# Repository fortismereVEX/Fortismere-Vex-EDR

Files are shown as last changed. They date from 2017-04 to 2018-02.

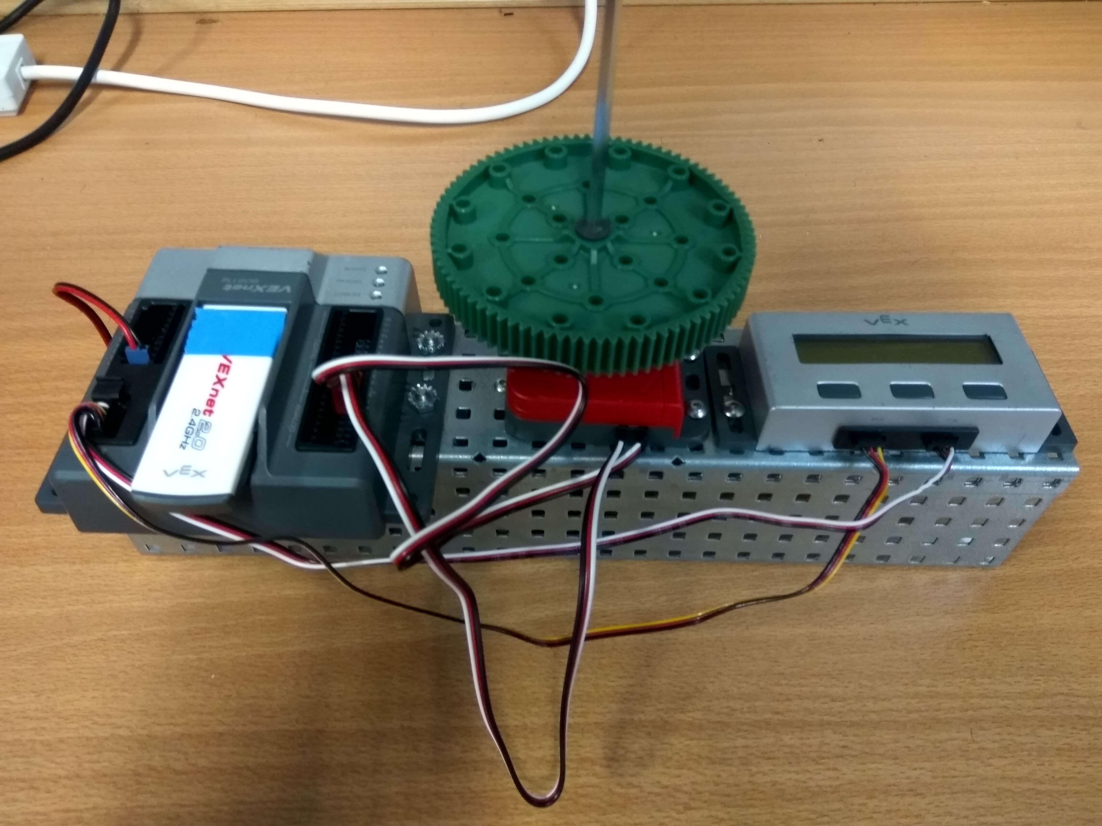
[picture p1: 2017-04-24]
zone/notebook/Resources/photos/PID Control.jpg

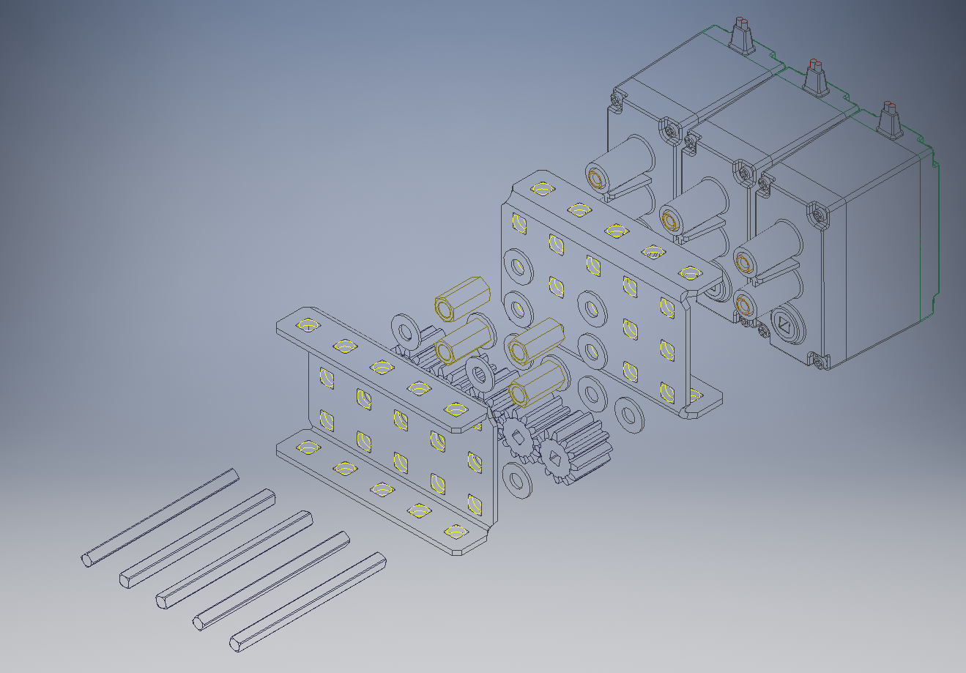
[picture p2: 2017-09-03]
zone/notebook/Renders and other cad stuff/Motor Block/Pictures and renders/Motor Block exploded view.PNG

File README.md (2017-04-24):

# Fortismere-Vex-EDR

Repo containing the various programs and tests for our Vex Robotics team, in addition to assorted files related to our engineering notebook.

##### /starstruck is for the 2016/2017 competition - Starstruck https://www.youtube.com/watch?v=0t2zstQ84Tw&t=1s
##### /zone is for the 2017/2018 competition  - In the Zone https://www.youtube.com/watch?v=1Yo_mlR1VJU

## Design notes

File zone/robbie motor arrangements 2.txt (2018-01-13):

1: mogo lift
2: claw left
3: left lift 1
4: exp 1 
5: exp 2
6: exp 3
7: exp 4
8: right lift 1
9: claw right
10: cone intake

expander:
1: drive right middle + drive right back
2: drive left middle + drive left back
3: left lift 2
4: right lift 2

sensors:
analogue:
2: left lift
3: right lift

digital:
2: + 3: left
4 + 5: right

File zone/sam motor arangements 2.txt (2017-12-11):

1 : arm left
2 : drive front left
3 : mogo right
4 : exp 1 
5 : exp 2
6 : exp 3
7 : exp 4
8 : lift 1
9 : drive front right
10: arm right

expander:
4 1: drive right middle + drive right back
5 2: drive left middle + drive left back
6 3: claw
7 4: mogo left

front left
middle left
back left
front right
middle right
back right
arm 1
arm 2
lift 1
claw
mogo 1
mogo 2

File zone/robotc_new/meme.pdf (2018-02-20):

File: C:\Users\admin\Documents\GitHub\Fortismere-Vex-EDR\zone\robotc_new\__basic.c

Page 1 of 11

#pragma config(Sensor, in1, left_line_sensor, | sensorLin

#pragma config(Sensor, in2, right_line_sensor, | sensorLi

#pragma config(Sensor, in3, claw_potent, | sensorPoten

#pragma config(Sensor, dgtl1, right_encoder, | sensorQuadE

#pragma config(Sensor, dgtl3, left_encoder, | sensorQuadE

#pragma config(Motor, port1, claw_1, | tmo

#pragma config(Motor, port2, right_front, | tmo

#pragma config(Motor, port3, left_front, | tmo

#pragma config(Motor, port4, arm_left_1, | tmo

#pragma config(Motor, port5, arm_left_2, | tmo

#pragma config(Motor, port6, arm_right_1, | tmo

#pragma config(Motor, port7, arm_right_2, | tmo

#pragma config(Motor, port8, right_back_middle,

#pragma config(Motor, port9, | left_back_middle,

#pragma config(Motor, port10, | claw_2, | tmo

//*!!Code automatically generated by 'ROBOTC' configuratio

#include "robotc_base_include.c"

#define max(x, a) (x > a ? x : a)

#define min(x, a) (x < a ? x : a) #define clamp(x, a, b) (min(b, max(a, x)))

float requested_left = 0.0;
float requested_right = 0.0;

float current_left = 0.0;
float current_right = 0.0;

float integral_left;
float integral_right;

float last_error_left;
float last_error_right;

float max_speed = 60.0;

void get_requested_delta(float *left, float *right) {

File: C:\Users\admin\Documents\GitHub\Fortismere-Vex-EDR\zone\robotc_new\__basic.c

Page 2 of 11

int r = (vexRT[Ch1] - vexRT[Ch3]);
int l = (vexRT[Ch1] + vexRT[Ch3]);

*left = abs(l) > 20 ? l : 0; *right = abs(r) > 20 ? r : 0;
}

float step_pid(float constant_p, float constant_i,
float constant_d,
float requested,
float current_value,
float *last_error,
float *integral) {
float error = current_value - requested;

float derivitive = error - *last_error; *last_error = error;

if (constant_i != 0 && abs(error) < 50) { *integral = *integral + error;
} else {
*integral = 0;
}

return constant_p * error + constant_i * *integral +
constant_d * derivitive;
}
task pid_loop() | {
// clear out the encoder
SensorValue[left_encoder] = 0; SensorValue[right_encoder] = 0;

current_left = 0;
current_right = 0;

File: C:\Users\admin\Documents\GitHub\Fortismere-Vex-EDR\zone\robotc_new\__basic.c

Page 3 of 11

requested_left = 0;
requested_right = 0;

last_error_left = 0;
last_error_right = 0;

integral_left = 0;
integral_right = 0;

bool reset = true;

while (true) {
current_left = SensorValue[left_encoder]; current_right = SensorValue[right_encoder];

/*
// user control stuff
float delta_requested_left = 0;
float delta_requested_right = 0;

get_requested_delta(&delta_requested_left, &delta_

if (delta_requested_left == 0 && delta_requested_r if (reset) {
requested_left = 0;
requested_right = 0;
SensorValue[left_encoder] = 0; SensorValue[right_encoder] = 0;

last_error_left = 0;
last_error_right = 0;

reset = false;
}
} else {
requested_left += delta_requested_left / 20; requested_right += delta_requested_right / 20;

File: C:\Users\admin\Documents\GitHub\Fortismere-Vex-EDR\zone\robotc_new\__basic.c

Page 4 of 11

reset = true;
}
*/

float new_left = step_pid(1, 0.0, 1, requested_left,
current_left,
&last_error_left,
&integral_left);
float new_right = step_pid(1, 0.0, 1, requested_right,
current_right,
&last_error_right,
&integral_right);

if (abs(new_left) < 20) new_left = 0;
if (abs(new_right) < 20) new_right = 0;

writeDebugStreamLine("r: %.2f %.2f c: %.2f %.2f e:

new_left = clamp(new_left, -max_speed, max_speed) new_right = clamp(new_right, -max_speed, max_speed

motor[right_front] = -new_right; motor[right_back_middle] = -new_right;

motor[left_front] = -new_left; motor[left_back_middle] = -new_left; }
}
void init() | {
stop_tasks_between_mode = true; }

void forward(float amount) {

File: C:\Users\admin\Documents\GitHub\Fortismere-Vex-EDR\zone\robotc_new\__basic.c

Page 5 of 11

requested_right -= amount;
requested_left += amount;
}
void turn(float amount) {
requested_right += amount; requested_left += amount;
}

bool at_dest(float threshold) {
if(abs(requested_left - current_left) < threshold | &&
abs(requested_right - current_right) < threshol integral_left = 0;
integral_right = 0;
return true;
}

return false;
}

void wait_for_dest(int timeout_ticks) { int curr = timeout_ticks;
while(!at_dest(20) && curr >= 0) { sleep(25);
--curr;
//clearLCDLine(0);
//displayLCDNumber(0, 0, curr, 2); }

if(curr == 0) {
displayLCDString(0, 0, "MISSED!!"); requested_left = current_left; requested_right = current_right; last_error_left = 0;
last_error_right = 0;
}
}

// positive for up, negative for down

File: C:\Users\admin\Documents\GitHub\Fortismere-Vex-EDR\zone\robotc_new\__basic.c

Page 6 of 11

void arm(int power) {
motor[arm_left_1] = -power;
motor[arm_left_2] = power;

motor[arm_right_1] = -power; motor[arm_right_2] = power; }

void claw(int power) {
motor[claw_1] = power;
motor[claw_2] = -power;
}

// TODO: all these timeouts are huge!!!
// The last one does at most 50 ticks before it gets to wh
task auton() | {
stopTask(pid_loop);
startTask(pid_loop);

SensorValue[claw_potent] = 0;

SensorValue[left_line_sensor] = 0; SensorValue[right_line_sensor] = 0;

int auton_option = 0;

bLCDBacklight = true;
clearLCDLine(0);
switch(auton_option) | {
case 0:
// Stack a cone onto the static goal

// move cone forward and then drive backwards

forward(100);
wait_for_dest(200);

File: C:\Users\admin\Documents\GitHub\Fortismere-Vex-EDR\zone\robotc_new\__basic.c

Page 7 of 11

forward(-100);
wait_for_dest(200);

arm(127);
sleep(300);
arm(0);
// claw close
claw(127);
sleep(500);
// arm down
claw(0);
arm(-127);
sleep(700)
arm(0);

// forwards
forward(100);
wait_for_dest(1000);

// claw close
claw(127);
sleep(800);
claw(30);

// arm up
arm(127);
sleep(800);
arm(0);

// forward
forward(250);
wait_for_dest(500);

sleep(800);

// arm down
arm(-127);
sleep(400);

File: C:\Users\admin\Documents\GitHub\Fortismere-Vex-EDR\zone\robotc_new\__basic.c

Page 8 of 11

// claw open
claw(-127);
sleep(400);
arm(0);
claw(0);

forward(-200);
wait_for_dest(100);
turn(150);
wait_for_dest(100);
forward(200);
wait_for_dest(100);
turn(-150);
wait_for_dest(100);
forward(600);
wait_for_dest(400);
}

stopTask(pid_loop);
all_motors_off();
}
enum | {
claw_open = 0,
claw_closed = 1,
}

int requested_claw = claw_closed;

task user_control() | {
//startTask(pid_loop);
SensorValue[claw_potent] = 0;

SensorValue[left_line_sensor] = 0; SensorValue[right_line_sensor] = 0;

sleep(500);

File: C:\Users\admin\Documents\GitHub\Fortismere-Vex-EDR\zone\robotc_new\__basic.c

Page 9 of 11

while (true) {
int r = (vexRT[Ch3] - vexRT[Ch1]); int l = (vexRT[Ch3] + vexRT[Ch1]);

if (abs(l) < 20) l = 0;
if (abs(r) < 20) r = 0;

motor[right_front] = -r;
motor[right_back_middle] = -r;

motor[left_front] = l;
motor[left_back_middle] = l;

int arm_sign = 0;
if(vexRT[Btn5U] == true) { arm_sign = 1;
} else if(vexRT[Btn5D] == true) { arm_sign = -1;
}

motor[arm_left_1] = 127 * -arm_sign; motor[arm_left_2] = 127 * arm_sign;

motor[arm_right_1] = 127 * -arm_sign; motor[arm_right_2] = 127 * arm_sign;

if(vexRT[Btn6U] == true) { requested_claw = claw_closed;
} else if(vexRT[Btn6D] == true) { requested_claw = claw_open;
}

if(requested_claw == claw_open) { if(SensorValue[claw_potent] > 2900) { motor[claw_1] = -127;
} else if(SensorValue[claw_potent] > 2800) { motor[claw_1] = -30;

File: C:\Users\admin\Documents\GitHub\Fortismere-Vex-EDR\zone\robotc_new\__basic.c

Page 10 of 11

} else {
motor[claw_1] = 0;
}
} else if(requested_claw == claw_closed) { if(SensorValue[claw_potent] < 3000) { motor[claw_1] = 127;
} else if(SensorValue[claw_potent] < 3100) { motor[claw_1] = 30;
} else if(SensorValue[claw_potent] < 3250) { motor[claw_1] = 30;
} else {
motor[claw_1] = 0; // we missed...
}
}

/*
int claw_sign = 0;
if(vexRT[Btn6U] == true) { claw_sign = 1;
} else if(vexRT[Btn6D] == true) { claw_sign = -1;
}
*/
bLCDBacklight = true;
clearLCDLine(0);
displayLCDNumber(0, 0, SensorValue[claw_potent], | 2

//motor[claw_1] = 127 * claw_sign; //motor[claw_2] = 127 * -claw_sign;

/*
if(SensorValue[left_line_sensor] < 2700 && SensorV bLCDBacklight = true;
} else {
bLCDBacklight = false;
}
*/

File: C:\Users\admin\Documents\GitHub\Fortismere-Vex-EDR\zone\robotc_new\__basic.c

Page 11 of 11

//clearLCDLine(0);
//displayLCDString(0, 0, "s: "); //displayNextLCDNumber(SensorValue[sonar], 3);

}

}

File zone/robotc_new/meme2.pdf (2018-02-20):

File: C:\Users\admin\Documents\GitHub\Fortismere-Vex-EDR\zone\robotc_new\__basic.c

Page 1 of 11

#pragma config(Sensor, in1, left_line_sensor, | sensorLin

#pragma config(Sensor, in2, right_line_sensor, | sensorLi

#pragma config(Sensor, in3, claw_potent, | sensorPoten

#pragma config(Sensor, dgtl1, right_encoder, | sensorQuadE

#pragma config(Sensor, dgtl3, left_encoder, | sensorQuadE

#pragma config(Motor, port1, claw_1, | tmo

#pragma config(Motor, port2, right_front, | tmo

#pragma config(Motor, port3, left_front, | tmo

#pragma config(Motor, port4, arm_left_1, | tmo

#pragma config(Motor, port5, arm_left_2, | tmo

#pragma config(Motor, port6, arm_right_1, | tmo

#pragma config(Motor, port7, arm_right_2, | tmo

#pragma config(Motor, port8, right_back_middle,

#pragma config(Motor, port9, | left_back_middle,

#pragma config(Motor, port10, | claw_2, | tmo

//*!!Code automatically generated by 'ROBOTC' configuratio

#include "robotc_base_include.c"

// utilitys for numbers
// unfortunately we do not have the safety of C++ template

#define max(x, a) (x > a ? x : a)

#define min(x, a) (x < a ? x : a)

#define clamp(x, a, b) (min(b, max(a, x)))

// These values are exposed here to allow helper functions float requested_left = 0.0;
float requested_right = 0.0;

float current_left = 0.0;
float current_right = 0.0;

float integral_left;
float integral_right;

float last_error_left;
float last_error_right;

File: C:\Users\admin\Documents\GitHub\Fortismere-Vex-EDR\zone\robotc_new\__basic.c

Page 2 of 11

float max_speed = 60.0;

void get_requested_delta(float *left, float *right) {
int r = (vexRT[Ch1] - vexRT[Ch3]);
int l = (vexRT[Ch1] + vexRT[Ch3]);

*left = abs(l) > 20 ? l : 0;
*right = abs(r) > 20 ? r : 0;
}

float step_pid(float constant_p, float constant_i,
float constant_d,
float requested,
float current_value,
float *last_error,
float *integral) {
float error = current_value - requested;

float derivitive = error - *last_error; *last_error = error;

if (constant_i != 0 && abs(error) < 50) { *integral = *integral + error;
} else {
*integral = 0;
}

return constant_p * error + constant_i * *integral +
constant_d * derivitive;
}
task pid_loop() | {
// clear out the encoder
SensorValue[left_encoder] = 0; SensorValue[right_encoder] = 0;

File: C:\Users\admin\Documents\GitHub\Fortismere-Vex-EDR\zone\robotc_new\__basic.c

Page 3 of 11

current_left = 0;
current_right = 0;

requested_left = 0;
requested_right = 0;

last_error_left = 0;
last_error_right = 0;

integral_left = 0;
integral_right = 0;

bool reset = true;

while (true) {
current_left = SensorValue[left_encoder]; current_right = SensorValue[right_encoder];

// Since pid is only used in autonomous this code /*
// get new usercontrol values here
float delta_requested_left = 0;
float delta_requested_right = 0;

get_requested_delta(&delta_requested_left, &delta_

if (delta_requested_left == 0 && delta_requested_r if (reset) {
requested_left = 0;
requested_right = 0;
SensorValue[left_encoder] = 0; SensorValue[right_encoder] = 0;

last_error_left = 0;
last_error_right = 0;

File: C:\Users\admin\Documents\GitHub\Fortismere-Vex-EDR\zone\robotc_new\__basic.c

Page 4 of 11

reset = false;
}
} else {
requested_left += delta_requested_left / 20; requested_right += delta_requested_right / 20;

reset = true;
}
*/

float new_left = step_pid(1, 0.0, 1, requested_left,
current_left,
&last_error_left,
&integral_left);
float new_right = step_pid(1, 0.0, 1, requested_right,
current_right,
&last_error_right,
&integral_right);

if (abs(new_left) < 20) new_left = 0;
if (abs(new_right) < 20) new_right = 0;

writeDebugStreamLine("r: %.2f %.2f c: %.2f %.2f e:

new_left = clamp(new_left, -max_speed, max_speed) new_right = clamp(new_right, -max_speed, max_speed

motor[right_front] = -new_right; motor[right_back_middle] = -new_right;

motor[left_front] = -new_left; motor[left_back_middle] = -new_left; }
}

File: C:\Users\admin\Documents\GitHub\Fortismere-Vex-EDR\zone\robotc_new\__basic.c

Page 5 of 11

void init() | {
stop_tasks_between_mode = true;
}

void forward(float amount) { requested_right -= amount; requested_left += amount;
}
void turn(float amount) {
requested_right += amount; requested_left += amount;
}

bool at_dest(float threshold) {
if(abs(requested_left - current_left) < threshold | &&
abs(requested_right - current_right) < threshol integral_left = 0;
integral_right = 0;
return true;
}

return false;
}

void wait_for_dest(int timeout_ticks) { int curr = timeout_ticks;
while(!at_dest(20) && curr >= 0) { sleep(25);
--curr;
//clearLCDLine(0);
//displayLCDNumber(0, 0, curr, 2); }

if(curr == 0) {
displayLCDString(0, 0, "MISSED!!"); requested_left = current_left; requested_right = current_right; last_error_left = 0;

File: C:\Users\admin\Documents\GitHub\Fortismere-Vex-EDR\zone\robotc_new\__basic.c

Page 6 of 11

last_error_right = 0;
}
}

// positive for up, negative for down void arm(int power) {
motor[arm_left_1] = -power; motor[arm_left_2] = power;

motor[arm_right_1] = -power; motor[arm_right_2] = power; }

void claw(int power) {
motor[claw_1] = power;
motor[claw_2] = -power;
}
task auton() | {
// Make sure the pid loop is restarted properly // This will get rid of residue
stopTask(pid_loop);
startTask(pid_loop);

// Clear other sensors that we might use in the future SensorValue[claw_potent] = 0; SensorValue[left_line_sensor] = 0; SensorValue[right_line_sensor] = 0;

// potential for new
int auton_option = 0;

bLCDBacklight = true;
clearLCDLine(0);
switch(auton_option) | {
case 0:
// Stack a cone onto the static goal

File: C:\Users\admin\Documents\GitHub\Fortismere-Vex-EDR\zone\robotc_new\__basic.c

Page 7 of 11

// move cone forward and then drive backwards forward(100);
wait_for_dest(200);
forward(-100);
wait_for_dest(200);

// Lift the arm up so that the claw can be closed arm(127);
sleep(300);
arm(0);
// claw close
claw(127);
sleep(500);
// arm down
claw(0);
arm(-127);
sleep(700)
arm(0);

// drive forwards so that the claw is around the c forward(100);
wait_for_dest(1000);

// claw close
claw(127);
sleep(800);
claw(30);

// arm up
arm(127);
sleep(800);
arm(0);

// forward
forward(250);
wait_for_dest(500);

File: C:\Users\admin\Documents\GitHub\Fortismere-Vex-EDR\zone\robotc_new\__basic.c

Page 8 of 11

// wait for the rocking to subside before lowering sleep(1300);

// arm down
arm(-127);
sleep(400);

// claw open
claw(-127);
sleep(400);
arm(0);
claw(0);

// drive back
forward(-200);
wait_for_dest(100);

// close the claw so that it doesnt get stuck on t claw(127);
sleep(400);
claw(0);

// turn first away from the mobile goal turn(200);
wait_for_dest(300);
// and move forwards
forward(250);
wait_for_dest(300);

// then turn inwards towards the centre of the pit turn(-150);
wait_for_dest(300);
// and forwards
forward(600);
wait_for_dest(400);

break;
}

File: C:\Users\admin\Documents\GitHub\Fortismere-Vex-EDR\zone\robotc_new\__basic.c

Page 9 of 11

// Stop pid and stop all motors to prevent drifting ar
stopTask(pid_loop);
all_motors_off();
}

// states for the claw
enum | {
claw_open = 0,
claw_closed = 1,
}

int requested_claw = claw_closed;

task user_control() | {
SensorValue[claw_potent] = 0;

SensorValue[left_line_sensor] = 0; SensorValue[right_line_sensor] = 0;

sleep(500);

while (true) {
// usercontrol movement
// we dont run pid in drivercontrol as the driftin // movement
int r = (vexRT[Ch3] - vexRT[Ch1]);
int l = (vexRT[Ch3] + vexRT[Ch1]);

// account for deadzone
if (abs(l) < 20) l = 0;
if (abs(r) < 20) r = 0;

motor[right_front] = -r;
motor[right_back_middle] = -r;

motor[left_front] = l;
motor[left_back_middle] = l;

File: C:\Users\admin\Documents\GitHub\Fortismere-Vex-EDR\zone\robotc_new\__basic.c

Page 10 of 11

// move the arm
int arm_sign = 0;
if(vexRT[Btn5U] == true) { arm_sign = 1;
} else if(vexRT[Btn5D] == true) { arm_sign = -1;
}

motor[arm_left_1] = 127 * -arm_sign; motor[arm_left_2] = 127 * arm_sign;

motor[arm_right_1] = 127 * -arm_sign; motor[arm_right_2] = 127 * arm_sign;

// move the claw
if(vexRT[Btn6U] == true) { requested_claw = claw_closed;
} else if(vexRT[Btn6D] == true) { requested_claw = claw_open;
}

if(requested_claw == claw_open) { if(SensorValue[claw_potent] > 2900) { // close motor[claw_1] = -127;
} else if(SensorValue[claw_potent] > 2800) { / motor[claw_1] = -30;
} else {
motor[claw_1] = 0;
}
} else if(requested_claw == claw_closed) { if(SensorValue[claw_potent] < 3000) { // open motor[claw_1] = 127;
} else if(SensorValue[claw_potent] < 3100) { / motor[claw_1] = 30;
} else if(SensorValue[claw_potent] < 3250) { / motor[claw_1] = 30;
} else {

File: C:\Users\admin\Documents\GitHub\Fortismere-Vex-EDR\zone\robotc_new\__basic.c

Page 11 of 11

motor[claw_1] = 0; // we missed... }
}

/*
// Test code for the line sensors if(SensorValue[left_line_sensor] < 2700 && SensorV bLCDBacklight = true;
} else {
bLCDBacklight = false;
}
*/
}

}

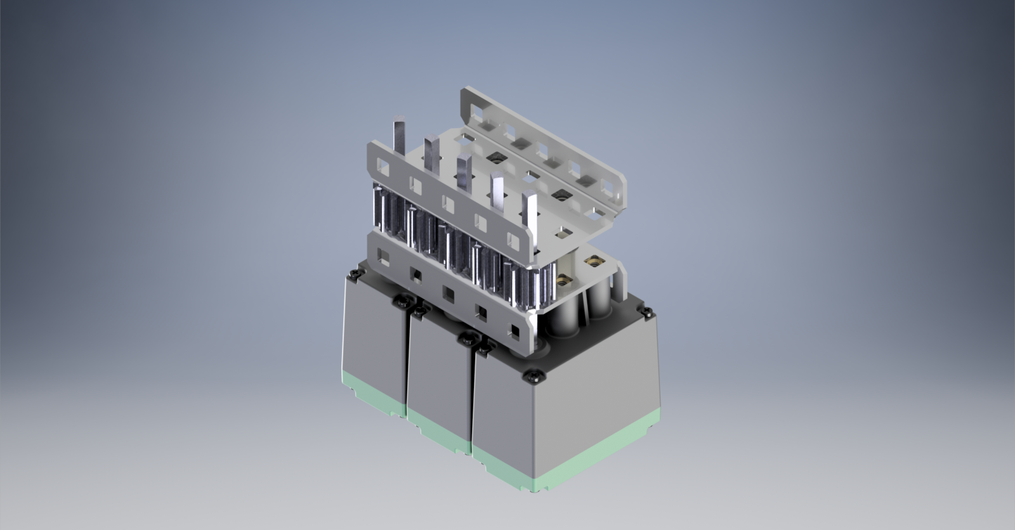
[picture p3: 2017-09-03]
zone/notebook/Renders and other cad stuff/Motor Block/Pictures and renders/Motor Block render.png

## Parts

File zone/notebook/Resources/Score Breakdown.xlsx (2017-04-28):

Category | Name | Indivdual points | Amount | Overall points | Percentage | Difficulty
Autonomous | Win | 10 | 1 | 10 | 6.289308176
Cones | On Field | 2 | 26 | 52 | 32.70440252
Cones | Preload | 2 | 2 | 4 | 2.51572327
Cones | Driver Load | 2 | 12 | 24 | 15.09433962
Mobile Goal | 20pt Zone | 20 | 1 | 20 | 12.57861635
Mobile Goal | 10pt Zone | 10 | 3 | 30 | 18.86792453
Highest Stack | 20pt Zone | 5 | 1 | 5 | 3.144654088
Highest Stack | 10pt Zone | 5 | 1 | 5 | 3.144654088
Highest Stack | Static Goal | 5 | 1 | 5 | 3.144654088
Park Bonus | Team square | 2 | 2 | 4 | 2.51572327
Total | Everything |  |  | 159 | 100
Autonomous | All | 10 | 1 | 10 | 6.289308176
Cones | All | 2 | 40 | 80 | 50.31446541
Mobile Goal | All |  |  | 50 | 31.44654088
Highest Stack | All | 5 | 3 | 15 | 9.433962264
Park Bonus | All | 2 | 2 | 4 | 2.51572327

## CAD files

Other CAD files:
zone/notebook/Renders and other cad stuff/Motor Block/CADs and other files/Drive Block exploaded view.ipn
zone/notebook/Renders and other cad stuff/Motor Block/CADs and other files/Drive Block.iam

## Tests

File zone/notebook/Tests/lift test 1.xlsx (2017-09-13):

Number of Cones | No bands | Two bands | Four Bands | Six bands
0 |  |  | Yes
1
2
3
4
5
6
7
8
9
10
11
12
13
14
15
16

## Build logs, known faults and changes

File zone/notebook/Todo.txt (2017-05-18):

//How this works///////////////////////////////////////////////////
Add something if it needs to be done, remove it if you have done it
///////////////////////////////////////////////////////////////////
- Explain Discord (How we chat and where we steal our ideas from)
- Explain Github
- Explain Code IDE (The one Josh is using for C++)
- Explain the PID thing we worked on
- Look at game strats

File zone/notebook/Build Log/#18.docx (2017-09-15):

# Robot v1.31

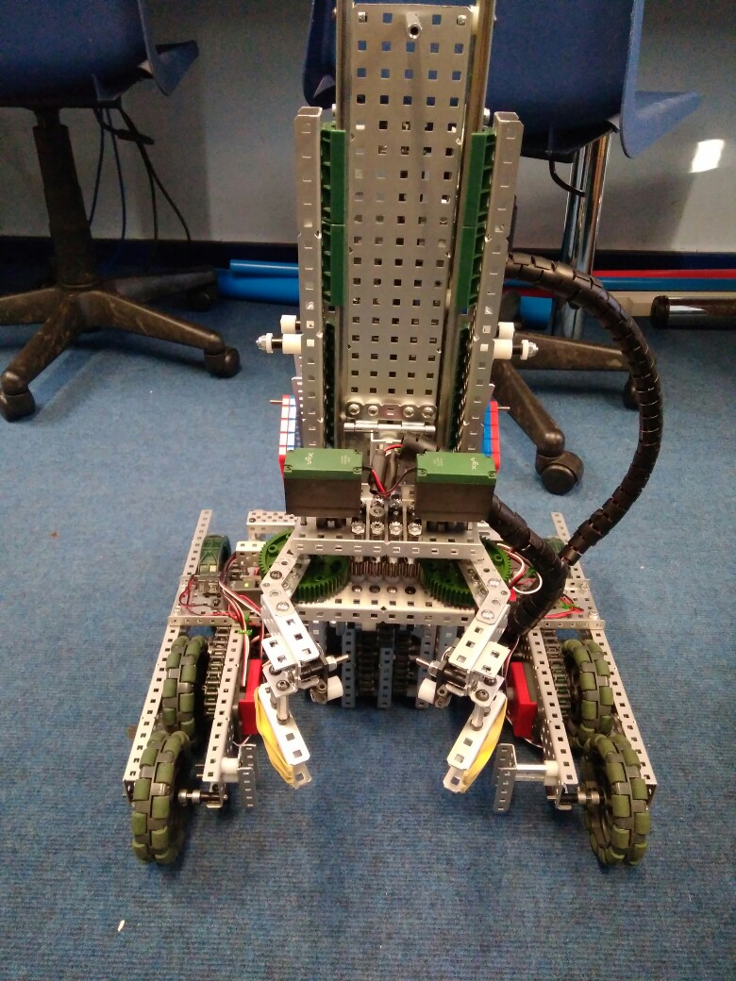
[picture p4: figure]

Specification:

- 6 Motor HS drive
- 2 drive chains
- 4 omni – 2 friction wheels
- Aluminium structure
- 4 motor lift
- 3 stage lift
- 2 motor flip down claw
- 5.5kg weight

Dimensions:

- 17.5” x 17.5” x 17.5” when not extended

Logged by Sam Poirier

15/09/2017 – 11:13

Future Changes:

- Program PID control
- Add limiter switches again

Overview:

There hasn’t been much visible progress over the last 20 days due to the fact that team has started school again and has not have much time available to spend working on vex. However, we did manage to get a few things fixed. We switched out the back omni-wheels for traction wheels to be assist the robot going over the bars. We also managed to fix the drive problem (as shown in problem log 3 on page #). The last thing we did was adjust the mogo (mobile goals) section of the claw to be better at picking up mogos by shortening it and by adding rubber bands for grip.

Changes Made:

- Fixed drive problem
- Moved over to pros for software development
- Replaced rear wheels with friction wheels
- Rebuilt claw

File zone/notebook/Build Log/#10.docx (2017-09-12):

# Robot v1.23

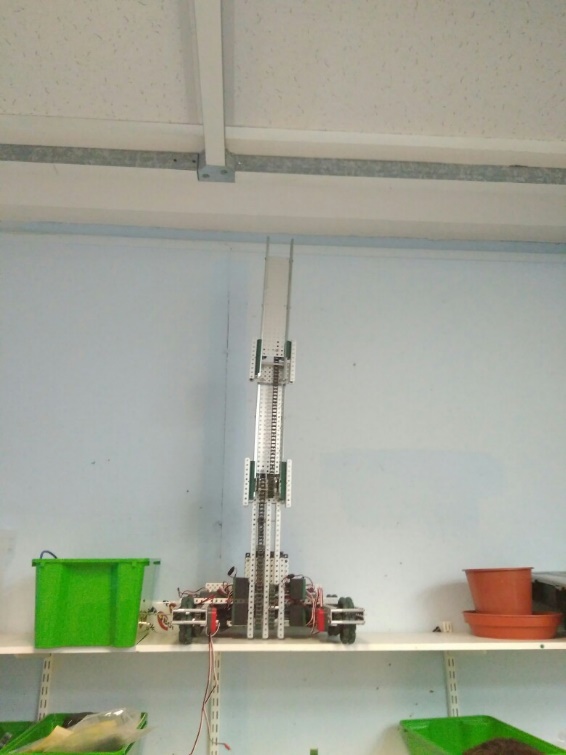
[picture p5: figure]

Specification:

- 6 Motor HS drive
- 2 drive chains
- 4 wheels
- Aluminium structure
- 4 motor lift
- 3 stage lift
- 2 motor claw

Dimensions:

- 17.5” x 15” x 17.5” when not extended

Logged by Robbie Buxton

17/07/2017 – 16:30

Overview:

The parts we needed to make the third stage finally arrived (two 12 tooth sprockets) today so we could complete the third stage of lift. The linear action works very well however it a bit lop-sided which is something we will need to fix. After we mount the claw the core robot will be finished and we will be able to focus on fine tuning the robot.

Future Changes:

- Plug in shaft encoders
- Make lift straight
- Mount claw

Changes Made:

- Added third stage

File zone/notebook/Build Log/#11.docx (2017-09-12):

# Robot v1.24

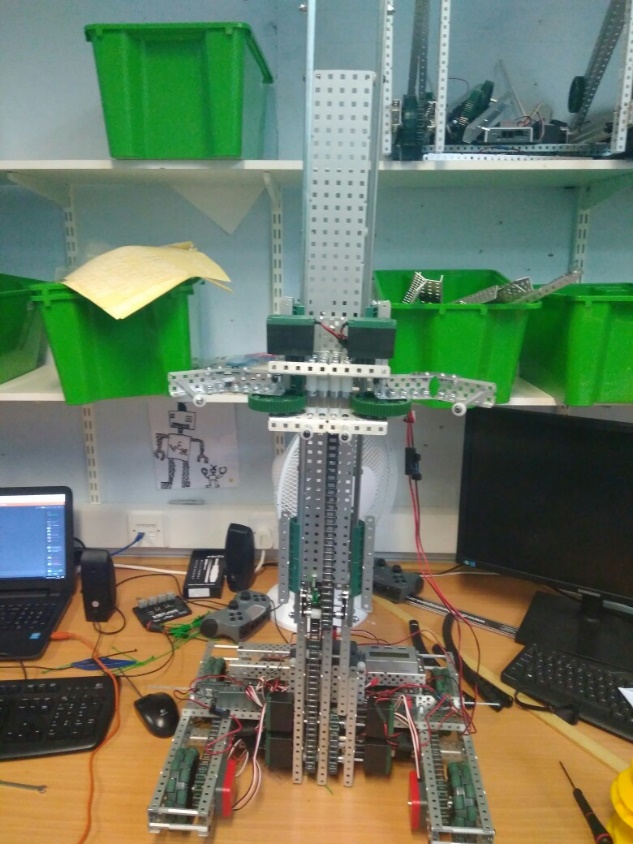
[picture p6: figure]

Specification:

- 6 Motor HS drive
- 2 drive chains
- 4 wheels
- Aluminium structure
- 4 motor lift
- 3 stage lift
- 2 motor claw

Dimensions:

- 17.5” x 15” x 17.5” when not extended

Overview:

For this version of the robot we have remounted the claw. We also managed to fix the problem with the robot being slanted by loosening then tightening all the screws holding the lift in place. We have found that when the robot starts to lift heavier weights the main chain in the lift begins to skip gears. This is a huge problem if we cannot fix it as it basically invalidates the main idea behind the design; being a multi-role robot able to lift mobile goals in addition to cones on the same lift. As well as fixing that problem we also need do some cable management and plug the shaft encoders in.

Logged by Felix Black

18/07/2017 – 16:12

Future Changes:

- Plug in shaft encoders
- Fix chain skipping problem
- Cable management

Changes Made:

- Mounted claw
- Straightened lift mechanism

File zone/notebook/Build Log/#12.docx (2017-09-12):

# Robot v1.25

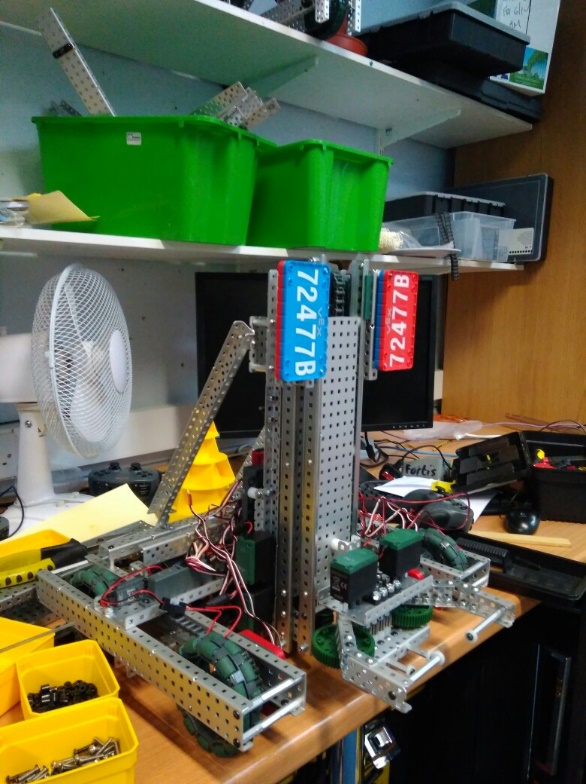
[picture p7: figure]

Specification:

- 6 Motor HS drive
- 2 drive chains
- 4 wheels
- Aluminium structure
- 4 motor lift
- 3 stage lift
- 2 motor claw

Dimensions:

- 17.5” x 15” x 17.5” when not extended

Logged by Sam Poirier

19/07/2017 – 17:06

Overview:

Most of the time spent this session was focused on trying to fix the chain skipping problem which we finally fixed. For more details on the problem have a look at the 2nd problem document on page (###). Along with fixing that major problem we also experimented with adding two support struts behind the lift to give it greater stability. They turned out to be quite useful so we have made them part of the key structure. We also located a place to initially mount the number plates. It is important that it is easy to swap out the colours for when we enter a competition. The place they currently reside looks nice however is not very practical as it only shows the robots number from a single direction so we will need to move them to opposing sides of the robot.

Future Changes:

- Plug in shaft encoders
- Cable manages
- Put number plates in a better position

Changes Made:

- Fixed chain skipping problem
- Added number plates
- Added two support bars

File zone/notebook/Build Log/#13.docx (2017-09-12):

# Robot v1.26

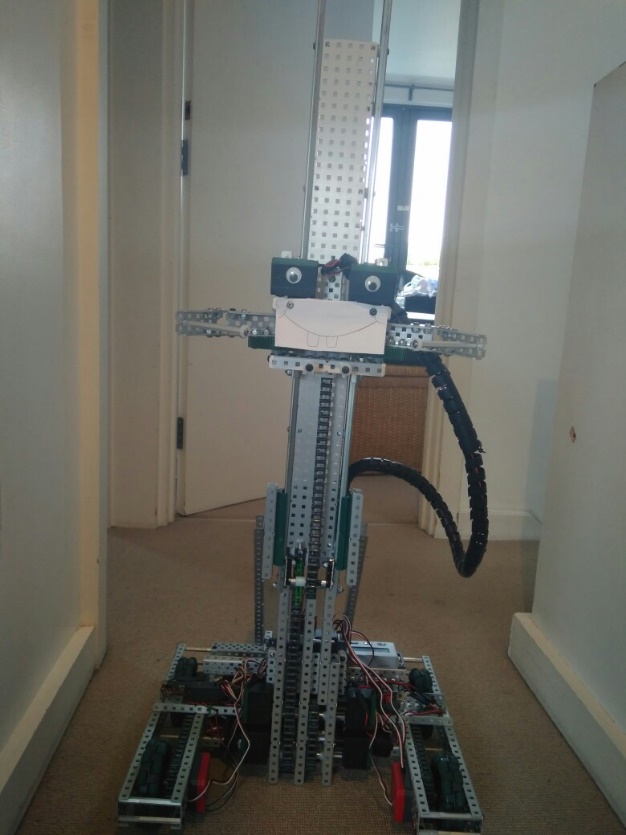
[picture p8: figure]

Specification:

- 6 Motor HS drive
- 2 drive chains
- 4 wheels
- Aluminium structure
- 4 motor lift
- 3 stage lift
- 2 motor claw

Dimensions:

- 17.5” x 15” x 17.5” when not extended

Logged by Sam Poirier

20/07/2017 – 19:51

Overview:

Most of the day was spend transporting the robot from school to Robbie’s house because we have decided to work on it over the summer there, however we did get some word done on the robot. The first thing we did was to properly secure all the cables on the robot to stop them getting stuck in resulting in a complete breakdown. We also put some casing around the main wire from the cortex to claw so it doesn’t get suck on parts of the robot and get pulled out with lifting. We also added two line trackers for later in the season when we start to work on autonomous allowing for a more accurate and intelligent program and finally plugged in all the peripherals so we have no loose wires.

Future Changes:

- Put number plates in a better position
- Redesign claw

Changes Made:

- Added cosmetics
- Done cable management
- Added two-line tracks
- Plugged in peripherals

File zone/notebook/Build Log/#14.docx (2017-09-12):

# Robot v1.27

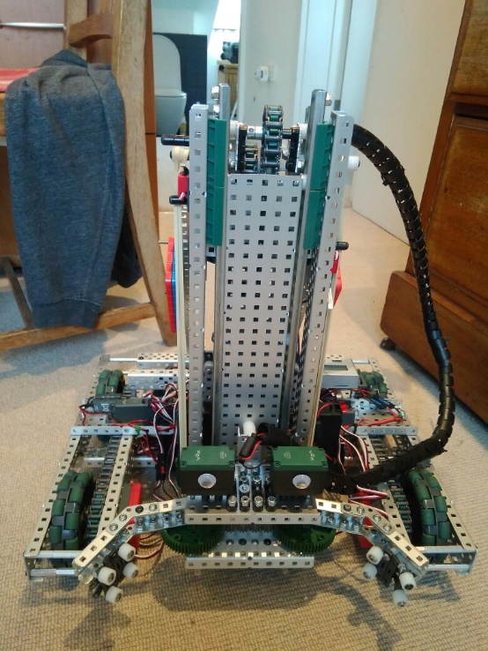
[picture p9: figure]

Specification:

- 6 Motor HS drive
- 2 drive chains
- 4 wheels
- Aluminium structure
- 4 motor lift
- 3 stage lift
- 2 motor claw

Dimensions:

- 17.5” x 15” x 17.5” when not extended

Logged by Robbie Buxton

30/07/2017 – 20:36

Overview:

The robot is now nearly ready to enter the full programming phase as most of the engineering work is complete. The first things we added today were two limit switches allowing us to program the lift to cut out at the minimum and maximum heights and an integrated motor encoder enabling us to implement PID control to the lift. We also added a Potentiometer to the claw so we can later also implement PID control there. The next thing we did was to rebuild the claw. We removed the standoffs and replaced them with spacers on tank tread which are far better at gripping the cone. We still need to add the module to the claw to manipulate mobile goals however since they still haven’t arrived yet we need to wait until they arrive before we can accurately do that. The final thing we did today was to add rubber bands to assist the lift. This allows it to be faster and stronger when going upwards which is essential as our lift is multifunctional and needs to be able to lift a whole stack.

What needs to be changed:

- Add mobile goal manipulator element to claw
- Program PID control
- Add stabilisers

Changes Made:

- Added integrated motor encoders
- Added two limit switches to the lift
- Remade the claw
- Put number plates in a better position
- Added elastic bands to assist lift.
- Added Potentiometer to the claw

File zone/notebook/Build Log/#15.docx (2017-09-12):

# Robot v1.28

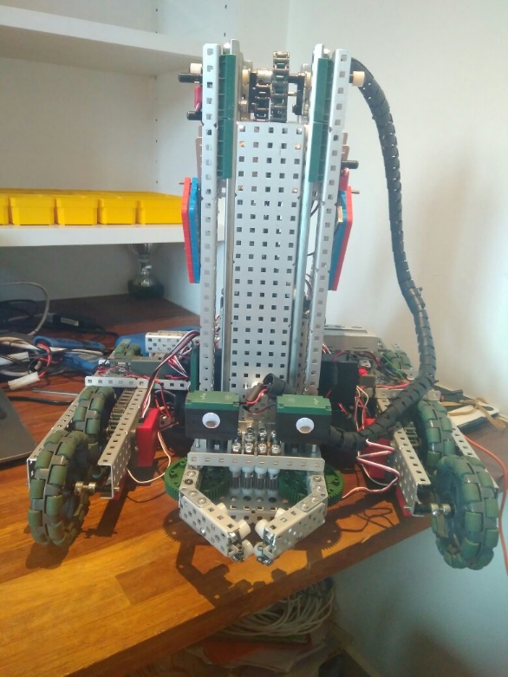
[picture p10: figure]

Specification:

- 6 Motor HS drive
- 2 drive chains
- 6 wheels
- Aluminium structure
- 4 motor lift
- 3 stage lift
- 2 motor claw

Dimensions:

- 17.5” x 15” x 17.5” when not extended

Logged by Sam Poirier

02/08/2017 – 11:54

Overview:

For this version of the robot we managed to fix two problems with one change. The first problem was that the robot was unstable and very prone to falling over. The second problem is that we realised is that if the robot tries to go over the bar into the 10 point zone the bottom of the lift will get caught on the bar and will result in the robot getting stuck. We think we fixed both these problems by moving the front wheels into the centre of the robot and added a new pair of free-wheeling wheels at the very front to increase the size of the base of the robot therefore increasing stability. By moving the wheels to the centre when the robot passes over the bar the wheels should also be touching bar instead of the lift stopping it getting stuck. We have not been able to test this however because our field elements still have not arrived in the UK.

Future Changes:

- Add mobile goal manipulator element to claw
- Program PID control

Changes Made:

- Added extra pair of wheels for stability
- Moved front wheels to the middle

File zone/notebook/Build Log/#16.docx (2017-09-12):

# Robot v1.29

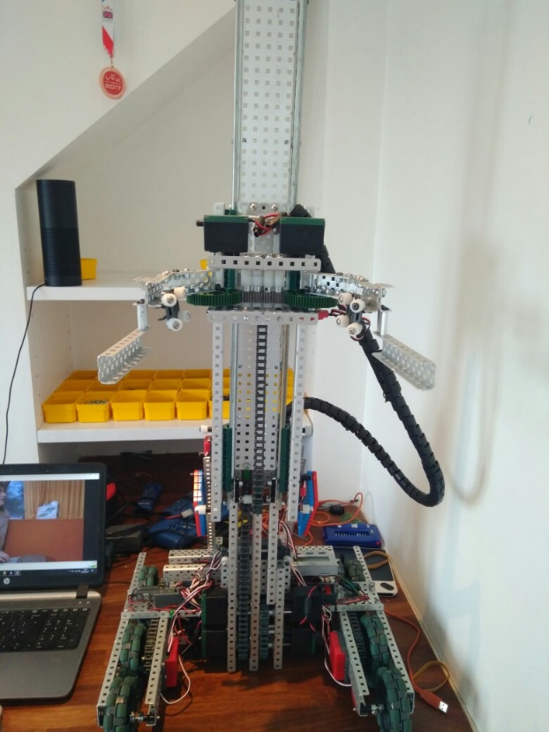
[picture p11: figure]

Specification:

- 6 Motor HS drive
- 2 drive chains
- 6 wheels
- Aluminium structure
- 4 motor lift
- 3 stage lift
- 2 motor flip down claw

Dimensions:

- 17.5” x 17.5” x 17.5” when not extended

Logged by Felix Black

04/08/2017 – 16:03

Future Changes:

- Program PID control
- Add a way to hold up claw before the match starts

Overview:

After we called up our Vex parts supplier we found out that our field elements would not be arriving for at least another month. We decided to cut out a piece of paper in the exact dimensions of the mobile goal found in the field appendixes to try and prototype a mobile goal manipulator. After building the extension to the claw which we are certain will be able to pick up the mobile goal we realized that the claw was too big and was out of the size limit. After deciding that making it smaller wouldn’t be a very good idea we decided to make our claw fold up at the begging. We did this using a hinge. We now need to find out a way to hold the claw up before the match starts.

Changes Made:

- Added mobile goal manipulator
- Made the claw flip down

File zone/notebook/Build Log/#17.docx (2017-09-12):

# Robot v1.30

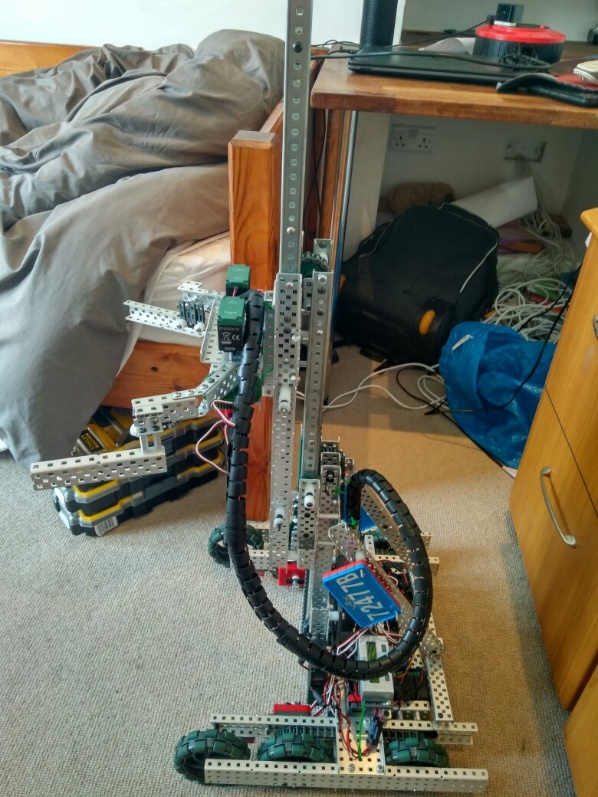
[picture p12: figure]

Specification:

- 6 Motor HS drive
- 2 drive chains
- 6 wheels
- Aluminium structure
- 4 motor lift
- 3 stage lift
- 2 motor flip down claw
- 5.5kg weight

Dimensions:

- 17.5” x 17.5” x 17.5” when not extended

s

Logged by Robbie Buxton

25/08/2017 – 10:09

Future Changes:

- Program PID control
- Fix drive problem
- Add limiter switches again

Overview:

Over the last 20 days we had a bit of a break from working on the robot as some team members had holidays and it was not possible to organize build sessions. The focus of this update was reworking the rubber band system so we could reliably lift the mobile goal as we were having trouble with it earlier. We moved the primary rubber band system closer together and added a counter rubber band system to hold the robot inside the size limit at the begging of the match. The counter rubber band system is released by moving the robot forward as it is attached to a rotating lock bar on the wheel axle. We also extended the bar used to stop chain skipping under both chains. While adjusting the rubber band systems we also temporary removed the limiter switches. One of the problems with the robot that we noticed is that the drive shorts out quickly when driving. We fiddled with the drive to try and reduce friction but that did not seem to have much effect. We need to fix this quite urgently because it renders the robot nearly useless.

Changes Made:

- Reworked rubber band system on the lift
- Added counter rubber band system
- Added rubber band releases
- Minor adjustments inside drive
- The bar used to stop chain skipping has been expanded to both chains
- Temporarily removed limiter switches

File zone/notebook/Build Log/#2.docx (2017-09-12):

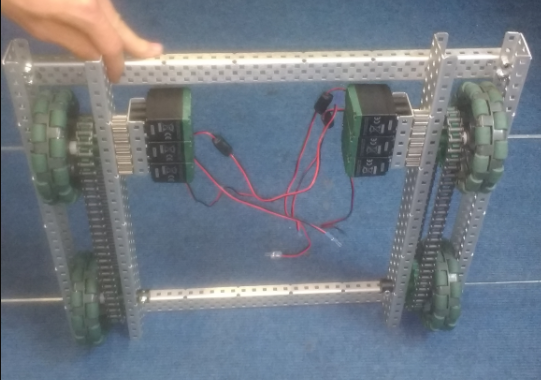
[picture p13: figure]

Logged by Sam Poirier

20/06/2017 – 16:14

Future Changes:

- Axles need to be cut and secured
- Need to add a plate for mounting the lifting device/intake

Changes Made:

- Motors have been moved from the primary frame to a secondary mounting
- 2 internal wheels have been removed

Overview:

This is the second version of our robot. With the first prototype, we found that too much space was being wasted allowing all the motors to be blocked together, reducing the space in the centre of the robot which we needed for our intake device. We decided to make the motor block a modular attachment. We will most likely keep this basic design for the next versions of the robot however it requires some additions and changes such as securing axles and the addition of a mounting plate for our lifting device.

We removed two wheels as doubling them up was unnecessary and only served to add redundant weight to the robot.

Specification:

- 6 Motor HS drive
- 2 drive chains
- 4 wheels
- Aluminium structure

Dimensions:

- 17.5″ x 15″

# Robot v1.02

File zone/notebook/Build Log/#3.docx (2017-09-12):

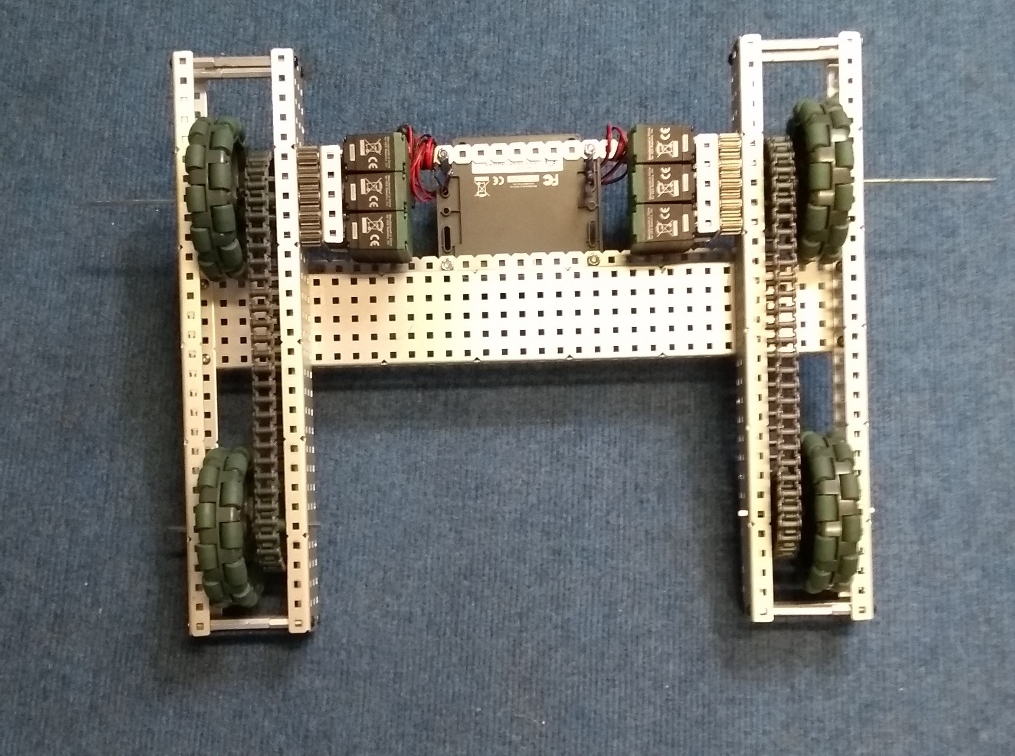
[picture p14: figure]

Overview:

This is only as small change to the prior version of the robot. None of the internal mechanism have been changed as the focus of this version was to modify the base to have a strong but light structure. Each of the wheel sections are now independently held together by stand-offs meaning that access to the wheel areas for modification of the mechanisms or structure is easier. The temporary structs on each end of the robot have also been replaced with a single bar across the middle allowing the base to be able to intake objects in the front without them being caught.

Logged by Robbie Buxton

21/06/2017 – 16:38

Future Changes:

- A battery mount needs to be built, with the ability to swap out charged and uncharged batteries with ease
- The mounting plate on the top needs to be added

Changes Made:

- The method that the chassis is held together by has been changed
- Basis for mounting plate added
- Shaft collars added to lock wheels into the robot

Specification:

- 6 Motor HS drive
- 2 drive chains
- 4 wheels
- Aluminium structure

Dimensions:

- 17.5” x 15”

# Robot v1.03

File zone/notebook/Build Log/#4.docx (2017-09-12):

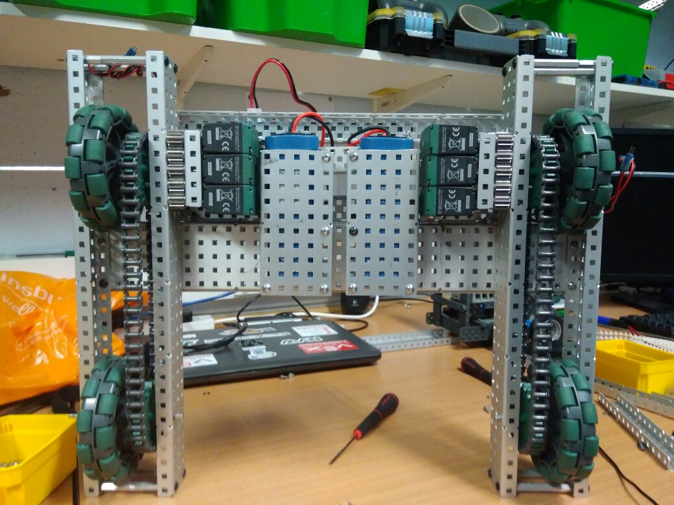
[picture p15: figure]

Specification:

- 6 Motor HS drive
- 2 drive chains
- 4 wheels
- Aluminium structure

Dimensions:

- 17.5” x 15”

Changes Made:

- Added 2 battery mounts
- Added the front mounting plate for the lift mechanism
- Securely mounted the brain and power extender
- Added a method to secure the batteries when the robot is active

Future Changes:

- Cable Management!
- Start work on the primary and secondary lift

# Robot v1.04

Overview:

The next addition is a device for storing batteries. A large 10 x 5 C section is suspended by 3 stand-offs. The batteries can be easily slipped in and out then secured by tightening a securing bar. The batteries are then plugged into two cable extenders that are plugged in respectively to the cortex and the power extender. We have also added a large plate for the primary lift to be mounted upon. The cortex mounting has been replaced with a more reliable system and a power extender has been added. After everything is wired in the base will be fully functioning.

Logged by Felix Black

28/06/2017 – 17:12

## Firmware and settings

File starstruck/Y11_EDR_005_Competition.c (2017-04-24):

#pragma config(Sensor, dgtl1,  ArmEncoder,     sensorQuadEncoder)
#pragma config(Motor,  port1,           ClawL,         tmotorVex393_HBridge, openLoop)
#pragma config(Motor,  port2,           LiftLD,        tmotorVex393HighSpeed_MC29, openLoop)
#pragma config(Motor,  port3,           LiftRD,        tmotorVex393HighSpeed_MC29, openLoop, reversed)
#pragma config(Motor,  port4,           DriveL1,       tmotorVex393HighSpeed_MC29, openLoop)
#pragma config(Motor,  port5,           DriveL2,       tmotorVex393HighSpeed_MC29, openLoop)
#pragma config(Motor,  port6,           DriveL3,       tmotorVex393HighSpeed_MC29, openLoop)
#pragma config(Motor,  port7,           DriveR1,       tmotorVex393HighSpeed_MC29, openLoop, reversed)
#pragma config(Motor,  port8,           DriveR2,       tmotorVex393HighSpeed_MC29, openLoop, reversed)
#pragma config(Motor,  port9,           DriveR3,       tmotorVex393HighSpeed_MC29, openLoop, reversed)
#pragma config(Motor,  port10,          ClawR,         tmotorVex393_HBridge, openLoop, reversed)
//*!!Code automatically generated by 'ROBOTC' configuration wizard               !!*//

// This code is for the VEX cortex platform
#pragma platform(VEX2)

// Select Download method as "competition"
#pragma competitionControl(Competition)

//Main competition background code...do not modify!
#include "Vex_Competition_Includes.c"

#define MAX(x, y) (((x) > (y)) ? (x) : (y))
#define MIN(x, y) (((x) < (y)) ? (x) : (y))

// autonomous helpers
void ZeroDrive()
{
	int power = 0;
	// Left
	motor[DriveL1] = power;
	motor[DriveL2] = power;
	motor[DriveL3] = power;

	//Right
	motor[DriveR1] = power;
	motor[DriveR2] = power;
	motor[DriveR3] = power;
}

void ZeroClaw()
{
	int power = 0;

	motor[ClawL] = power;
	motor[ClawR] = power;
}

void ZeroArm()
{
	int power = 0;

	motor[LiftLD] = power;
	motor[LiftRD] = power;
}

void MoveForward(int time)
{
	int power = 127;
	// Left
	motor[DriveL1] = power;
	motor[DriveL2] = power;
	motor[DriveL3] = power;

	//Right
	motor[DriveR1] = power;
	motor[DriveR2] = power;
	motor[DriveR3] = power;

	sleep(time);

	ZeroDrive();
}

void MoveForward()
{
	int power = 127;
	// Left
	motor[DriveL1] = power;
	motor[DriveL2] = power;
	motor[DriveL3] = power;

	//Right
	motor[DriveR1] = power;
	motor[DriveR2] = power;
	motor[DriveR3] = power;
}

void MoveBackwards(int time)
{
	int power = 127;
	// Left
	motor[DriveL1] = -power;
	motor[DriveL2] = -power;
	motor[DriveL3] = -power;

	//Right
	motor[DriveR1] = -power;
	motor[DriveR2] = -power;
	motor[DriveR3] = -power;

	sleep(time);

	ZeroDrive();
}

void MoveBackwards()
{
	int power = 127;
	// Left
	motor[DriveL1] = -power;
	motor[DriveL2] = -power;
	motor[DriveL3] = -power;

	//Right
	motor[DriveR1] = -power;
	motor[DriveR2] = -power;
	motor[DriveR3] = -power;
}

void TurnLeft(int time)
{
	int power = 127;
	// Left
	motor[DriveL1] = -power;
	motor[DriveL2] = -power;
	motor[DriveL3] = -power;

	//Right
	motor[DriveR1] = power;
	motor[DriveR2] = power;
	motor[DriveR3] = power;

	sleep(time);

	ZeroDrive();
}

void TurnLeft()
{
	int power = 127;
	// Left
	motor[DriveL1] = -power;
	motor[DriveL2] = -power;
	motor[DriveL3] = -power;

	//Right
	motor[DriveR1] = power;
	motor[DriveR2] = power;
	motor[DriveR3] = power;
}

void TurnRight(int time)
{
	int power = 127;
	// Left
	motor[DriveL1] = power;
	motor[DriveL2] = power;
	motor[DriveL3] = power;

	//Right
	motor[DriveR1] = -power;
	motor[DriveR2] = -power;
	motor[DriveR3] = -power;

	sleep(time);

	ZeroDrive();
}

void TurnRight()
{
	int power = 127;
	// Left
	motor[DriveL1] = power;
	motor[DriveL2] = power;
	motor[DriveL3] = power;

	//Right
	motor[DriveR1] = -power;
	motor[DriveR2] = -power;
	motor[DriveR3] = -power;
}

void ClawOpen(int time)
{
	int power = 60;

	motor[ClawL] = -power;
	motor[ClawR] = -power;

	sleep(time);

	ZeroClaw();
}

void ClawOpen()
{
	int power = 60;

	motor[ClawL] = -power;
	motor[ClawR] = -power;
}

void ClawClose(int time)
{
	int power = 60;

	motor[ClawL] = power;
	motor[ClawR] = power;

	sleep(time);

	ZeroClaw();
}

void ClawClose()
{
	int power = 60;

	motor[ClawL] = power;
	motor[ClawR] = power;
}

void ArmUp(int time)
{
	int power = 127;

	motor[LiftLD] = power;
	motor[LiftRD] = power;

	sleep(time);
	ZeroArm();
}

void ArmUp()
{
	int power = 127;

	motor[LiftLD] = power;
	motor[LiftRD] = power;
}

void ArmDown(int time)
{
	int power = 127;

	motor[LiftLD] = -power;
	motor[LiftRD] = -power;

	sleep(time);
	ZeroArm();
}

void ArmDown()
{
	int power = 127;

	motor[LiftLD] = -power;
	motor[LiftRD] = -power;
}

void StartClaw()
{
	// you should run this to setup the claw for autnomous
	motor(ClawL) = 127;
	motor(ClawR) = 127;
	sleep(20);
	motor(ClawL) = -127;
	motor(ClawR) = -127;
	sleep(20);
	motor(ClawL) = 127;
	motor(ClawR) = 127;
	sleep(200);
	ArmUp();
	sleep(50);
	ZeroArm();
	sleep(400);
	ArmDown();
	ZeroClaw();
	sleep(50);
	ClawOpen();
	sleep(400);
	ZeroClaw();
	ZeroArm();
}

void AutonomousCubeLeft()
{

	StartClaw();

	ArmDown();
	sleep(200);
	ZeroArm();
	MoveForward(850);
	ClawClose();
	sleep(1000);

	TurnRight();
	ArmUp();
	sleep(500);

	MoveBackwards();

	ArmUp();


	sleep(1000);

	ZeroDrive();
	ZeroArm();

	ClawOpen();
	sleep(50);
	ZeroClaw();

}

void AutonomousCubeRight()
{
  StartClaw();

	ArmDown();
	sleep(200);
	ZeroArm();

	MoveForward(850);

	ClawClose();
	sleep(1000);

	TurnLeft();

	ArmUp();
	sleep(500);


	MoveBackwards();

	ArmUp();


	sleep(1000);

	ZeroDrive();

	ZeroArm();

	ClawOpen();
	sleep(50);

	ZeroClaw();
}

void AutonomousGeneric()
{
	StartClaw();
	sleep(200);
	ClawClose();
	sleep(60);
	ZeroClaw();
	ArmUp();
	MoveForward();
	sleep(650);
	ZeroArm();
	sleep(1400);
	ZeroDrive();
}
void amazingDriverSkills()
{
	StartClaw();
	MoveBackwards();
	sleep(250);
	int i = 0;
	for(i=0; i<3; i++)
	{
		ZeroDrive();
		sleep(3000);
		ClawClose();
		sleep(1000);
		ArmUp();
		//sleep(600); new sleep time below - delete if wrong
		sleep(800);
		MoveBackwards();
		//sleep(900); new sleep time below - delete if wrong
		sleep(1200);
		ZeroDrive();
		ZeroArm();
		ClawOpen();
		sleep(100);
		ZeroClaw();
		MoveForward();

		sleep(600);
		ArmDown();
		sleep(1400);
		ZeroDrive();
		ZeroArm();
	}
	ArmUp();
	ZeroDrive();
	sleep(500);
	ZeroArm();
	sleep(200);
	MoveForward();
	sleep(800);
	ZeroDrive();
	sleep(200);
	MoveBackwards();
	sleep(700);
	ZeroDrive();
	sleep(200);
	ArmDown();
	sleep(380);
	ArmUp();
	sleep(30);
	ZeroArm();
	sleep(200);
	TurnLeft();
	sleep(290);
	ZeroDrive();
	sleep(200);
	MoveForward();
	sleep(2000);
	ArmDown();
	sleep(50);
	ZeroArm();
	sleep(1000);
	ZeroDrive();
	sleep(200);
	ClawClose();
	sleep(400);
	TurnRight();
	sleep(450);
	ZeroDrive();
	sleep(200);
	ArmUp();
	sleep(900);
	MoveBackwards();
	sleep(600);
	ClawOpen();
	sleep(200);
	ZeroClaw();
	ZeroArm();
	ZeroDrive();
	MoveBackwards();
	ArmDown();
	sleep(1000);
	ZeroDrive();
	TurnLeft();
	ArmDown();
	sleep(580);
	ZeroDrive();
	ClawOpen();
	sleep(1000);
	ZeroClaw();
	AutonomousGeneric();
	//sleep(500);
	//ClawOpen();
	//TurnLeft();
	//sleep(50);
	//ZeroClaw();
	//sleep(230);
	//ZeroDrive();
	//MoveForward();
	//sleep(500);
	//ClawClose();
	//sleep(600);
	//TurnRight();
	//ArmUp();
	//sleep(500);

	//MoveBackwards();

	//ArmUp();


	//sleep(1000);

	//ZeroDrive();
	//ZeroArm();

	//ClawOpen();
	//sleep(50);
	//ZeroClaw();
}


// for movement
// 500 is 30 inches (including drifting) 1 square

// for turning
// 100 is 90/4
// 250 is 90

typedef enum k_autonomous_debug
{
	AUTONOMOUS_TURN_RIGHT = 0,
	AUTONOMOUS_TURN_LEFT,
	AUTONOMOUS_FORWARD,
	AUTONOMOUS_BACKWARD,
	AUTONOMOUS_ARM_UP,
	AUTONOMOUS_ARM_DOWN,
	AUTONOMOUS_CLAW_OPEN,
	AUTONOMOUS_CLAW_CLOSE,
	AUTONOMOUS_DEBUG_LAST,
} autonomous_debug_t;

string autonomous_debug_strings[] =
{
	"TURN_RIGHT",
	"TURN_LEFT",
	"FORWARD",
	"BACKWARD",
	"ARM_UP",
	"ARM_DOWN",
	"CLAW_OPEN",
	"CLAW_CLOSE"
};


// ============================================================
// COMPETITION AUTONOMOUS
// ============================================================

// TODO: Fix this - cube left mode and fix the menu system to use correct types

typedef enum k_autonomous_mode
{
	AUTONOMOUS_GENERIC = 0,
	AUTONOMOUS_CUBE_RIGHT,
	AUTONOMOUS_CUBE_LEFT,
	AUTONOMOUS_DEBUG,
	AMAZING_PROG,
	AUTONOMOUS_MODE_LAST,
} autonomous_mode_t;

string autonomous_mode_strings[] =
{
	"generic",
	"cube right",
	"cube left",
	"debug",
	"prog skill",
};

// global for the autonomous mode selected
// the default autonomous mode is generic
// TODO: change this if we need to
autonomous_mode_t g_autonomous_mode = AUTONOMOUS_GENERIC;

void pre_auton()
{
  // Set bStopTasksBetweenModes to false if you want to keep user created tasks
  // running between Autonomous and Driver controlled modes. You will need to
  // manage all user created tasks if set to false.
  bStopTasksBetweenModes = false;

	// Set bDisplayCompetitionStatusOnLcd to false if you don't want the LCD
	// used by the competition include file, for example, you might want
	// to display your team name on the LCD in this function.
	bDisplayCompetitionStatusOnLcd = false;

  bLCDBacklight = true;

  int buttonsPressed = 0;

 	bool buttonsEqual = 0;

	int time;

	//while(true)
	//{
	//	sleep(100);
	//	buttonsPressed = nLCDButtons;

	//	// right button cycles through modes
	//	// center button selects them
	//	// debug mode is its own autonomous mode
	//	if(buttonsPressed == 4)
	//	{
	//		g_autonomous_mode = (g_autonomous_mode + 1) % AUTONOMOUS_MODE_LAST;
	//	}
	//	else if(buttonsPressed == 2)
	//	{
	//		// when the button is pressed twice in a row it is selected
	//		clearLCDLine(0);
	//		displayLCDString(0, 0, autonomous_mode_strings[g_autonomous_mode]);
	//		clearLCDLine(1);
	//		displayLCDString(0, 0, "selected");
	//		break;
	//		//Safety feature - Stop LCD control because the game has entered driver control mode
	//	if (!(bIfiAutonomousMode || bIfiRobotDisabled))
	//	{
	//			break;
	//	}

	//	}

		// display the currently selected mode from the list
		//clearLCDLine(0);
		//displayLCDString(0, 0, autonomous_mode_strings[g_autonomous_mode]);

		//clearLCDLine(1);
		//displayLCDString(1, 0, "Press center to select...");
	//}
}

task autonomous()
{
	//if(g_autonomous_mode == AUTONOMOUS_GENERIC)
	//{
		amazingDriverSkills();
	//}
	//else if(g_autonomous_mode == AUTONOMOUS_CUBE_LEFT)
	//{
	//	AutonomousCubeLeft();
	//}
	//else if(g_autonomous_mode == AUTONOMOUS_CUBE_RIGHT)
	//{
	//	AutonomousCubeRight();
	//}
	//else if(g_autonomous_mode == AMAZING_PROG)
	//{
	//	amazingDriverSkills();
	//}
	//else if(g_autonomous_mode == AUTONOMOUS_DEBUG)
	//{
	//	int buttonsPressed = 0;

	//	int time;

	//	autonomous_debug_t mode;

	//	while(true)
	//	{

	//		do
	//		{
	//			sleep(100);
	//			buttonsPressed = nLCDButtons;

	//			if(buttonsPressed == 5)
	//			{
	//				mode = (mode + 1) % AUTONOMOUS_DEBUG_LAST;
	//			}
	//			else if(buttonsPressed == 1)
	//			{
	//				time -= 10;
	//			}
	//			else if(buttonsPressed == 4)
	//			{
	//				time += 10;
	//			}

	//			clearLCDLine(0);
	//			clearLCDLine(1);
	//			displayLCDString(0, 0, autonomous_debug_strings[mode]);
	//			displayLCDNumber(1, 0, time);
	//		}
	//		while(buttonsPressed != 2);

	//		if(mode == AUTONOMOUS_TURN_RIGHT)
	//		{
	//			TurnRight(time);
	//		}
	//		else if(mode == AUTONOMOUS_TURN_LEFT)
	//		{
	//			TurnLeft(time);
	//		}
	//		else if(mode == AUTONOMOUS_FORWARD)
	//		{
	//			MoveForward(time);
	//		}
	//		else if(mode == AUTONOMOUS_BACKWARD)
	//		{
	//			MoveBackwards(time);
	//		}
	//		else if(mode == AUTONOMOUS_ARM_UP)
	//		{
	//			ArmUp(time);
	//		}
	//		else if(mode == AUTONOMOUS_ARM_DOWN)
	//		{
	//			ArmDown(time);
	//		}
	//		//these two are inverted for some reason.... ? -Sam
	//		else if(mode == AUTONOMOUS_CLAW_OPEN)
	//		{
	//			ClawClose(time);
	//		}
	//		else if(mode == AUTONOMOUS_CLAW_CLOSE)
	//		{
	//			ClawOpen(time);
	//		}
	//	}
	//}
}

task usercontrol()
{
  // User control code here, inside the loop
  bool closeSwitch = false;
	int toggle = 1;
	int clawTick = 0;

	//int encoderAcc = 0;

  //Clear Encoders
  SensorValue[ArmEncoder] = 0;

  string mainBattery, backupBattery;

  while (true)
  {
  	if (vexRT[Btn7L])
  	{
  		// clear the lcd display
	  	clearLCDLine(0);
			clearLCDLine(1);

			// Display the Primary Robot battery voltage
			displayLCDString(0, 0, "Primary: ");
			sprintf(mainBattery, "%1.2f%c", nImmediateBatteryLevel/1000.0,'V'); //Build the value to be displayed
			displayNextLCDString(mainBattery);

			// Display the Backup battery voltage
			displayLCDString(1, 0, "Backup: ");
			sprintf(backupBattery, "%1.2f%c", BackupBatteryLevel/1000.0, 'V');    //Build the value to be displayed
			displayNextLCDString(backupBattery);

			// Short delay for the LCD refresh rate
			// do we really want to be doing this? this will block this thread -
			// resulting in us being unable to use the robot for this time period
			wait1Msec(100);
		}

  	//sprintf(lcdDisplay, "%f", SensorValue[ArmEncoder]);
    //encoderAcc += SensorValue[ArmEncoder];
    displayLCDNumber(0, 0, SensorValue[ArmEncoder]);
    //SensorValue[ArmEncoder] = 0;

    int l = (vexRT[Ch3] + vexRT[Ch1]);
		int r = (vexRT[Ch3] - vexRT[Ch1]);

		float flForward = vexRT[Ch3];
		float flSide = vexRT[Ch1];

		int clawSpeed = 127;
		//Left
		motor[DriveL1] = l;
		motor[DriveL2] = l;
		motor[DriveL3] = l;
		//Right
		motor[DriveR1] = r;
		motor[DriveR2] = r;
		motor[DriveR3] = r;
		//Arm
		if (vexRT[Btn5U]) //Up
		{
			motor[LiftRD] = 127;
			motor[LiftLD] = 127;
		}
		else if (vexRT[Btn5D]) //Down
		{
			motor[LiftRD] = -127;
			motor[LiftLD] = -127;
		}
		else //Stop
		{
			motor[LiftRD] = 0;
			motor[LiftLD] = 0;
		}
		//Claw
		if (vexRT[Btn6U]) // Close
		{
			if(clawTick > 1000)
			{
				clawSpeed -= MIN(50, clawTick);
			}
			motor[ClawR] = clawSpeed;
			motor[ClawL] = clawSpeed;
			closeSwitch = false;
			clawTick += 1;

		}
		else if (vexRT[Btn6D]) // Open
		{
			if(clawTick > 1000)
			{
				clawSpeed -= MIN(50, clawTick);
			}
			motor[ClawR] = -clawSpeed;
			motor[ClawL] = -clawSpeed;
			//closeSwitch = true;
			clawTick += 1;

		}
		else //Stop
		{
			clawTick = 0;
			if (closeSwitch == false)
			{
				motor[ClawR] = 0;
				motor[ClawL] = 0;
			}

		if (vexRT(Btn7U))
		{
			motor[ClawR] = -127;
			motor[ClawL] = -127;
		}
			/*else
			{
				motor[ClawR] = -60;
				motor[ClawL] = -60;
			}
			*/
		}
  }
}

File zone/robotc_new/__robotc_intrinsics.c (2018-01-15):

////////////////////////////////////////////////////////////////////////////////////////////////
//
//                       Intrinsic Brick Instruction Implementations
//
// This file contains the detailed implementation code and definitions for
// RobotC intrinsics
//
////////////////////////////////////////////////////////////////////////////////////////////////

#include "ProgramType.h"
#include "PropertyTypes.h"
#include "DriveTrainTypes.h"
#include "EnumTypes.h"

#if defined(hasUserSerialPorts)
  #include "SerialPortEnums.h"
#endif

#if defined(bFirmwareStoresMotorType) || (bSmartMotorsWithEncoders() != 0) || defined(_WINDOWS)
  #include "TMotorTypes.h"
#endif

#if defined(bHasI2CPort) || defined(_WINDOWS)
	#include "I2CTypedefs.h"
#endif

typedef signed char byte;
typedef unsigned char ubyte;
typedef signed char sbyte;

typedef short word;

#define NULL ((void *) 0)


//////////////////////////////////////////////////////////////////////////////////////////
//
// Definition to 'ROBOTC' compiler of unique built-in variables used by the byte-code interpreter
//
//////////////////////////////////////////////////////////////////////////////////////////

//
// Syntax Example,
//    'intrinsic variable'      -- Compiler directive to define an internal "intrinsic" variable "array".
//    'globalVar'               -- the variable name known to the compiler.
//    'propertyVar'              -- the type of variable/parameter
//    'kNumbOfGlobalVariablesInBytes'  -- the size of the 'array' for these variables. If this is not specified
//                                 then a non-array variable is being used. e.g. 'clock', or 'message'
//                                 and can be referred to by any value
//
//    Item can now be referenced in 'ROBOTC' code with 'globalVar[23]', 'globalVar[i]', ... format
//

//
//    Note: There is an internal compiler 'kludge' so than 'random' is referred to as 'random(int)'
//          using round instead of curly brackets. Can't declare random as a 'function' because
//          assignment is allowed to set the random seed. The trick is to let 'random' be a variable
//          but it is referenced with round instead of curly brackets.
//

///////////////////////////////////////////////////////////////////////////////////////////////////////
//
//                              Task execution Control
//
///////////////////////////////////////////////////////////////////////////////////////////////////////

intrinsic void hogCPU()             asm(opcdSystemFunctions, byte(sysFuncHogProcessor));
intrinsic void releaseCPU()         asm(opcdSystemFunctions, byte(sysFuncFreeProcessor));
intrinsic void abortTimeslice()     asm(opcdSystemFunctions, byte(sysFuncSwitchContext));

///////////////////////////////////////////////////////////////////////////////////////////////////////
//
//                                memset and memcpy
//
///////////////////////////////////////////////////////////////////////////////////////////////////////

intrinsic void memcpy(void *pToBuffer, const void *pFromBuffer, const short nNumbOfBytes)
                      asm(opcdSystemFunctions, byte(sysFuncMemCpy),
                            variableRefVoidPtr(pToBuffer),
                            variableRefVoidPtr(pFromBuffer),
                            variable(nNumbOfBytes));

intrinsic void memset(void *pToBuffer, const char nValue, const short nNumbOfBytes)
                      asm(opcdSystemFunctions, byte(sysFuncMemSet),
                            variableRefVoidPtr(pToBuffer),
                            variable(nValue),
                            variable(nNumbOfBytes));

#if defined(hasMemMoveSupport)

intrinsic void memmove(void *pToBuffer, const void *pFromBuffer, const short nNumbOfBytes)
                      asm(opcdSystemFunctions, byte(sysFuncMemMove),
                            variableRefVoidPtr(pToBuffer),
                            variableRefVoidPtr(pFromBuffer),
                            variable(nNumbOfBytes));
#endif

#if defined(hasMemCmpSupport)

intrinsic short memcmp(const void *pToBuffer, const void *pFromBuffer, const short nNumbOfBytes)
                      asm(opcdSystemFunctions, byte(sysFuncMemCmp),
                            variableRefVoidPtr(pToBuffer),
                            variableRefVoidPtr(pFromBuffer),
                            variable(nNumbOfBytes),
														functionReturn);
#endif

///////////////////////////////////////////////////////////////////////////////////////////////////////
//
//                                "string" functions on byte arrays
//
///////////////////////////////////////////////////////////////////////////////////////////////////////

#if defined(hasStringSupport)

intrinsic void strcpy(char *pToBuffer, const char *pFromBuffer)
                      asm(opcdSystemFunctions, byte(sysFuncStrCpy),
                          variableRefCharPtr(pToBuffer),
                          variableRefCharPtr(pFromBuffer));

intrinsic void strcpy(string &pToBuffer, const char *pFromBuffer)
                      asm(opcdSystemFunctions, byte(sysFuncStrNCpy),
                          variableRefString(pToBuffer),
                          variableRefCharPtr(pFromBuffer),
                          constantValue(20));   // 'string' variable is 20 bytes long

intrinsic void strncpy(char *pToBuffer, const char *pFromBuffer, const short nMaxBufferSize)
                      asm(opcdSystemFunctions, byte(sysFuncStrNCpy),
                          variableRefCharPtr(pToBuffer),
                          variableRefCharPtr(pFromBuffer),
                          variable(nMaxBufferSize));

intrinsic void strcat(string &sToString, const char *pFromBuffer)
                      asm(opcdSystemFunctions, byte(sysFuncStrNCat),
                          variableRefString(sToString),
                          variableRefCharPtr(pFromBuffer),
                          constantValue(20));   // 'string' variable is 20 bytes long

intrinsic void strcat(char *pToBuffer, const char *pFromBuffer)
                      asm(opcdSystemFunctions, byte(sysFuncStrCat),
                          variableRefCharPtr(pToBuffer),
                          variableRefCharPtr(pFromBuffer));

intrinsic void strncat(char *pToBuffer, const char *pFromBuffer, const short nMaxBufferSize)
                      asm(opcdSystemFunctions,
                          byte(sysFuncStrNCat),
                          variableRefCharPtr(pToBuffer),
                          variableRefCharPtr(pFromBuffer),
                          variable(nMaxBufferSize));

intrinsic void strcatSingleChar(char &pToBuffer, const char cSingleChar)
                      asm(opcdSystemFunctions, byte(sysFuncStrCatSingleChar),
                          variableRefRAM(pToBuffer),
                          variable(cSingleChar));
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

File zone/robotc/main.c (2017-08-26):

#pragma config(Motor,  port1,           CL,            tmotorVex393_HBridge, openLoop, reversed)
#pragma config(Motor,  port2,           LL1,           tmotorVex393_MC29, openLoop, reversed)
#pragma config(Motor,  port3,           LL2,           tmotorVex393_MC29, openLoop, reversed)
#pragma config(Motor,  port4,           DL1,           tmotorVex393_MC29, openLoop)
#pragma config(Motor,  port5,           DL2,           tmotorVex393_MC29, openLoop)
#pragma config(Motor,  port6,           LR1,           tmotorVex393_MC29, openLoop)
#pragma config(Motor,  port7,           LR2,           tmotorVex393_MC29, openLoop)
#pragma config(Motor,  port8,           DR1,           tmotorVex393_MC29, openLoop, reversed)
#pragma config(Motor,  port9,           DR2,           tmotorVex393_MC29, openLoop, reversed)
#pragma config(Motor,  port10,          CR,            tmotorVex393_HBridge, openLoop)
//*!!Code automatically generated by 'ROBOTC' configuration wizard               !!*//

task main()
{
    while (true) {
    	//Drive
				int l = (vexRT[Ch3] + vexRT[Ch1]);
        int r = (vexRT[Ch3] - vexRT[Ch1]);
        //Left
        motor[DL1] = l;
        motor[DL2] = l;
        //Right
        motor[DR1] = r;
        motor[DR2] = r;
		//Lift
        //Up
        if (vexRT[Btn5D]) {
            motor[LL1] = 127;
            motor[LL2] = 127;
            motor[LR1] = 127;
            motor[LR2] = 127;
       }
       //Down
        else if (vexRT[Btn6D]) {
            motor[LL1] = -127;
            motor[LL2] = -127;
            motor[LR1] = -127;
            motor[LR2] = -127;
        }
        else {
            motor[LL1] = 0;
            motor[LL2] = 0;
            motor[LR1] = 0;
            motor[LR2] = 0;
        }
        //Claw
        //Open
        if (vexRT[Btn6U]) {
            motor[CL] = 60;
            motor[CR] = 60;
       	}
       	//Close
        else if (vexRT[Btn5U]) {
            motor[CL] = -60;
            motor[CR] = -60;
        }
        else {
            motor[CL] = 0;
            motor[CR] = 0;
    	}
	}
}

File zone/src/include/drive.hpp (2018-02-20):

#pragma once

#include "demo.hpp"
#include "lcd.hpp"
#include "main.hpp"

#include "motors.hpp"

class drive {
    static bool inited;

    // are we replaying joystick / button commmands
    static bool in_demo;
    static bool in_recording;

    static int last_time;

    static bool slow_mode;

    // other state
    static bool claw_open;
    static int  claw_power;

#ifdef ROBOT_ROBBIE
    static bool arm_up;
#endif

#ifdef ROBOT_SAM
    static pid_helper_real<ime> pid_drive_left;
    static pid_helper_real<ime> pid_drive_right;
#else
    static pid_helper_real<encoder> pid_drive_left;
    static pid_helper_real<encoder> pid_drive_right;
#endif

    static char  power_left;
    static char  power_right;
    static float requested_left;
    static float requested_right;

    static int get_delta_time() {
        int current_time = millis();
        int dt           = current_time - last_time;
        last_time        = current_time;
        return dt;
    }

public:
    static void initialize() {
        if (inited == true) return;

        // initialise imes
        imeShutdown();

        delay(1000);

        printf("==> imeInitializeAll()\n");
#ifdef ROBOT_SAM
        auto inited = imeInitializeAll();
#else
        auto inited = 0;
#endif
        printf("<=\n");

        lcd::printf("%d imes", inited);

// calibrate analogue sensors
#ifdef ROBOT_SAM
        analogCalibrate(8);
        // TODO: arm sensor
#elif defined(ROBOT_ROBBIE)
        // TODO: lift potentiometers
#endif
        inited = true;
    }

    static int get_joystick_analog(int axis) {
        if (in_demo == true) {
            // return next byte
            return 0;
        }

        char value = joystickGetAnalog(1, axis);

        // account for dead space
        // TODO: we shouldnt need to deal with this
        if (abs(value) < 20) value = 0;

        if (in_recording == true) {
            // write to buffer
        }

        return value;
    }
    static bool get_joystick_digital(int group, int direction) {
        if (in_demo == true) {
            // return next byte
            return 0;
        } else if (in_recording == true) {
            char value = joystickGetDigital(1, group, direction);
            // store value in buffer
            return value;
        }
        return joystickGetDigital(1, group, direction);
    }

    static void run_drive() {
        int fwd = get_joystick_analog(1);
        int lr  = get_joystick_analog(3);

        // @Hack for non pid travel
        power_right = (fwd - lr);
        power_left  = (fwd + lr);

        if ((fwd + lr) == 0) {
            // Tell pid that we no longer wish to move
            // reset to reset overall error that may have accumulated during travel
            pid_drive_left.reset();
            pid_drive_right.reset();
            pid_drive_left.set_requested(0);
            pid_drive_right.set_requested(0);
        } else {
            // ask pid to add this to our destination value
            pid_drive_left.set_requested(power_left);
            pid_drive_right.set_requested(power_right);
        }
    }

    static void run_intake() {
        // TODO: split into setting values here and
        // applying them in finalise to be consistent with other code
        if (get_joystick_digital(7, JOY_UP)) {
            motors::intake(127);
        } else if (get_joystick_digital(7, JOY_DOWN)) {
            motors::intake(-127);
        } else {
            motors::intake(0);
        }
    }

    static void run_lift() {
        if (get_joystick_digital(6, JOY_UP)) {
            motors::lift(127);
        } else if (get_joystick_digital(6, JOY_DOWN)) {
            motors::lift(-127);
        } else {
            motors::lift(0);
        }
    }

    static void run_arm() {
#ifdef ROBOT_SAM
        if (get_joystick_digital(8, JOY_UP)) {
            motors::arm(-127);
        } else if (get_joystick_digital(8, JOY_DOWN)) {
            motors::arm(127);
        } else {
            motors::arm(0);
        }
#else
        if (get_joystick_digital(5, JOY_UP)) {
            arm_up = true;
            motors::arm(-127);
        } else if (get_joystick_digital(5, JOY_DOWN)) {
            arm_up = false;
            motors::arm(127);
        } else {
            motors::arm(0);
        }
#endif
    }

    static void run_claw() {
#ifdef ROBOT_SAM
        lcdPrint(uart1, 2, "%d", analogReadCalibrated(8));
        // -50 to 50 full open
        // -800 to -900 is full close

        if (get_joystick_digital(5, JOY_UP)) {
            // open
            claw_open  = true;
            claw_power = 127;
        } else if (get_joystick_digital(5, JOY_DOWN)) {
            // close

            claw_open  = false;
            claw_power = -127;
        } else {
            claw_power = 0;
        }
#elif defined(ROBOT_ROBBIE)
        if (get_joystick_digital(8, JOY_UP)) {
            claw_open = true; // roll up

            motors::claw(127);

        } else if (get_joystick_digital(8, JOY_DOWN)) {
            claw_open = false; // roll down
            motors::claw(-127);
        } else {
            // if (claw_open) {
            //     motors::claw(15);
            // } else {
            //     motors::claw(-15);
            // }
            motors::claw(0);
        }
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

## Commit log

2016-12-05 arm programming started
2016-12-07 fix y11 edr code
    [Y11_EDR_001.c]
2016-12-08 Added motors
    Changed several motors to other ports, added motors for front wheels and
    claw.
2016-12-08 adjusted motor speeds
2017-01-19 fix problems with motor things
    [Y11_EDR_004.c]
2017-01-19 add my version of the motor code
2017-03-09 put current code into competition template
2017-03-14 Fix claw open/close bug
    [Y11_EDR_005_Competition.c]
2017-03-15 properly fix directional code
    [Y11_EDR_005_Competition.c]
2017-03-15 Add debug autonomous as its own autonomous program
    Right button to cycle
    Center button to select
2017-03-15 started generic autonomous and added claw debug options
2017-04-24 uploaded 'PID Control.jpg'
2017-04-27 Added Score breakdown
    [Score Breakdown.xlsx]
2017-04-28 add some pid control
2017-04-29 Added planetary gear system video
2017-07-19 Added Prototype code
    Prototpye code added
2017-07-30 Team Spreadsheet update
    title
    [Team Spreadsheet.xlsx]
2017-08-25 Finished plan and added build log
    [lift test 1.xlsx]
2017-08-26 Fixed code and added problem log
    [main.c, prototype.c]
2017-08-28 Added Event Timeline and fixed a doc
    [Team Spreadsheet.xlsx]
2017-09-03 Added render
    Added render and exploaded view for motor block as well as creating a
    folder for future renders
2017-09-03 Vex cad parts
    Added the actually cads and stuff to the folder
    [Drive Block exploaded view.ipn, Drive Block.iam]
2017-09-06 Fix pros lcd task - switching back to pros for further development
    [opcontrol.cpp]
2017-09-13 update code and docs
    [lift test 1.xlsx]
2017-09-14 Update library code
    [Drive Block exploaded view.ipn, Drive Block.iam, Score Breakdown.xlsx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]
2017-09-15 readd all files
    [Drive Block exploaded view.ipn, Drive Block.iam, Score Breakdown.xlsx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]
2017-09-16 Added Motor Block design doc
2017-11-06 Update lcd, opcontrol and makefile
    add pid and some other stuff
2017-11-08 Update pid
2017-11-10 Update pid and lcd code
2017-11-15 Update pid contants and rpm to power conversions
2017-11-16 generalise pid code to improve code reusability
2017-11-20 change drive ports update encoder get function to return a velocity
2017-11-29 add new pid code for autonomous
2017-11-30 Update drive motors and pid code
2017-12-07 Update motor arangements and pid code
2017-12-11 Update robot sam drive motors
2017-12-14 make claw a toggle switch for robot_sam
2018-01-22 update basic, main and motor_config
2018-02-20 Change some code split files fix robbie amazing
    [__basic_robbie.c, __basic_sam.c, auto.cpp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]
2018-02-27 lift pid meme
2018-03-01 robbie has an auton frame
2018-03-15 change pid code limits
